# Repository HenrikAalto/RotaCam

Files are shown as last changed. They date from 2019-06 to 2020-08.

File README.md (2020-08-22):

# RotorCam180

Mit dem Projekt <strong>RotorCam180</strong> soll eine drehbare WabCam erstellt werden. 
Basierend auf einem <em>ESP32CAM Modul</em> in Verbindung mit einem RC-Servo soll zunächst ein um 180° schwenkbares Kameramodul entstehen. Die Befehle zur Steuerung soll via Telnet gesendet werden können.

<strong>Motivation:</strong>  
Zwar gibt es eine Vielzahl an Webcams auf dem Markt, doch sind die allermeisten Modelle inzwischen nur mit einer herstellereigenen Cloud nutzbar. Eine Eigenheit die mir persönlich überhaupt nicht zusagt ;-)

<strong>Idee:</strong>  
Seit einiger Zeit ist nun das ESP32Cam-Modul verfügbar (z.B. bei <a href="https://www.banggood.com/Geekcreit-ESP32-CAM-WiFi-bluetooth-Camera-Module-Development-Board-ESP32-With-Camera-Module-OV2640-p-1394679.html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">Banggods</a>)
Die kompakte Bauform ist ideal um sie, in Kombination mit einem <a href="https://www.banggood.com/4-X-Towerpro-MG90S-Metal-Gear-RC-Micro-Servo-p-961967.html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">RC-Servo</a>, eine drehbare Webcam aufzubauen.

<strong>Umsetzung:</strong>  
Die eigentliche WebCam-Funktionalität ist bereits in diversen Repositories zur Verfügung gestellt worden. In der ersten Version greife ich auf SourceCode von <a href="https://randomnerdtutorials.com">RandomNerd</a> zurück. An dieser Stelle vielen Dank an Rui Santos!

Die Steuerung des Servos erfolgt über eine Telnet-Verbindung. Nach Eingabe eines ‚?‘ erscheint die aktuelle Befehlsliste:

<pre><code>ESP32 - Cam Controller V0.1.1 (04-06-2019)  
_________________________________________________________  
Befehle  
Bxxx    - Blitz (Intensität 0 < xxx < 100)  
Rxxx    - Rotation (Winkel 0 < xxx < 180  
q       - Telnet-Sitzung beenden  
l       - Zustandslog aktivieren/deaktivieren 
i       - Initialisierung  
?       - Diese Liste  
</code></pre>

<em>Hinweis:  
Die Kommando-Buchstaben (zur Steuerung des Moduls) sind in Großbuchstaben, gefolgt von einem Parameter, Sitzungsbefehle in Kleinbuchstaben einzugeben.</em>

Um eine solide Einheit zu bilden, braucht die ganze Geschichte natürlich ein kompaktes Gehäuse. Das STL-Files des Moduls liegt <a href="https://github.com/HenrikAalto/RotorCam180/blob/master/WebCam-Träger_v2.0.stl">hier</a> ab lässt sich mit einem 3D-Drucker leicht herstellen. Es dient lediglich als Basisträger. Eine Abdeckung die das Ganze wetterfest und damit für den Außeneinsatz tauglich machen wird, ist in Planung…

<strong>Technischen Details:</strong>  
Um den Aufbau möglichst schlank zu gestalten, also ohne zusätzliche Platine (die weiteren Platz gebraucht hätte), ist das Gehäuse so entworfen, dass es auf der einen Seite das ESP32CAM-Modul aufnimmt 
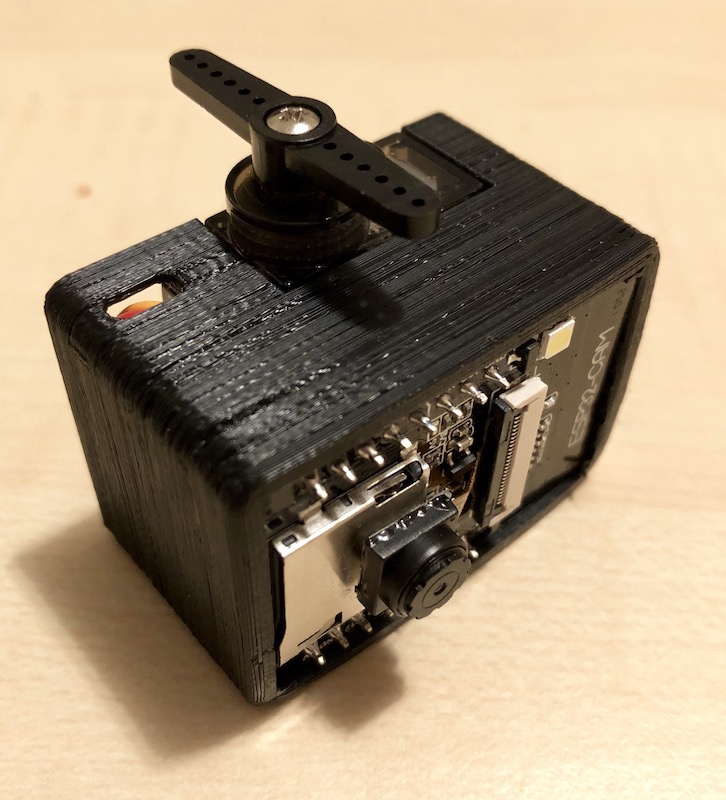
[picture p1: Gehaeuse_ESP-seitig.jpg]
  
und den Servo 
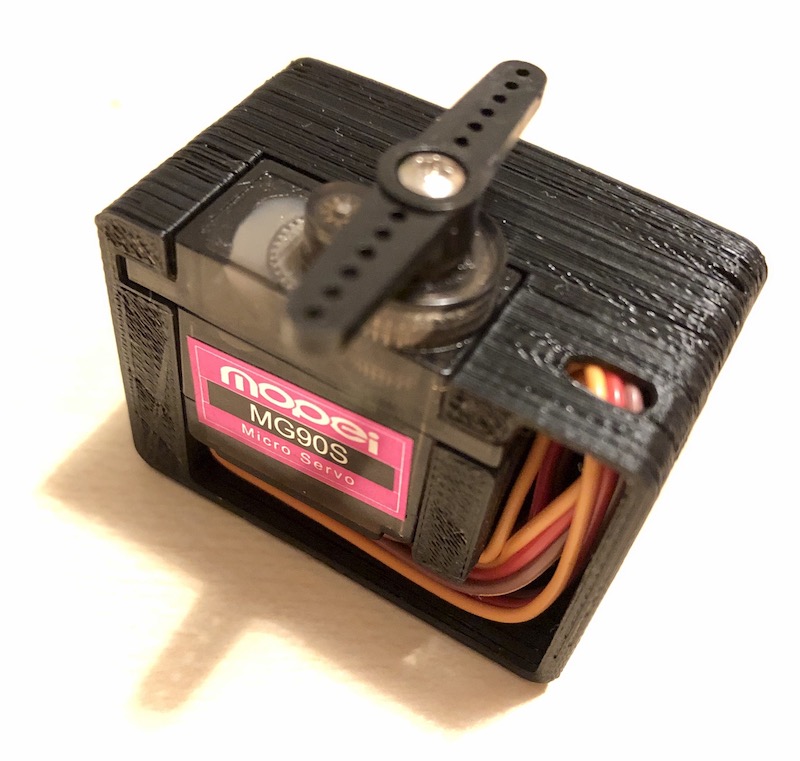
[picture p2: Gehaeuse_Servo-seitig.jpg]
  
auf der Anderen.  
Ein Durchbruch zu Vcc GND und Pin12 des ESP32CAM, in passender Größe für den Stecker des Servos ermöglichen die Verbindung von Beiden.  
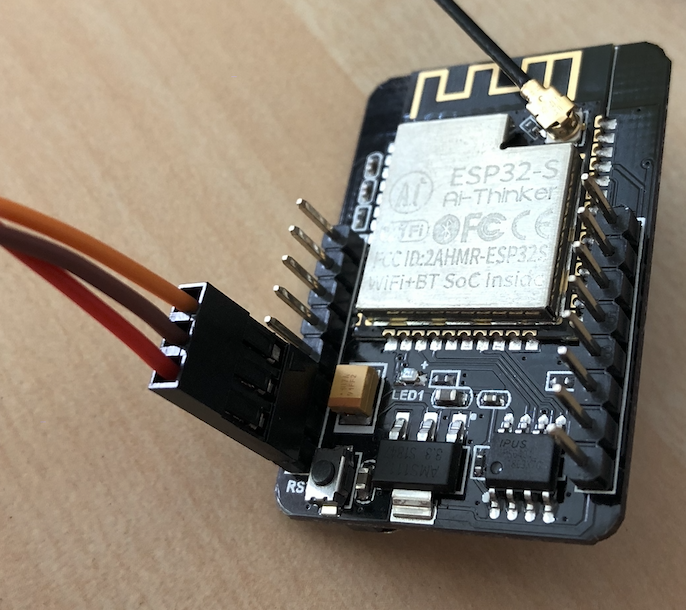
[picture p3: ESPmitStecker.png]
  
Leider passt die Pinbelegung des Steckers am Kabel Servomotor, bei diesem Modell nicht ab Werk nicht zu der am ESP32 CAM. Darum muss Vcc (rot) und GND (braun) am Stecker vertauscht werden. Es ist jedoch recht einfach die Kunststoffnasen des Steckers leicht aufzubiegen. 
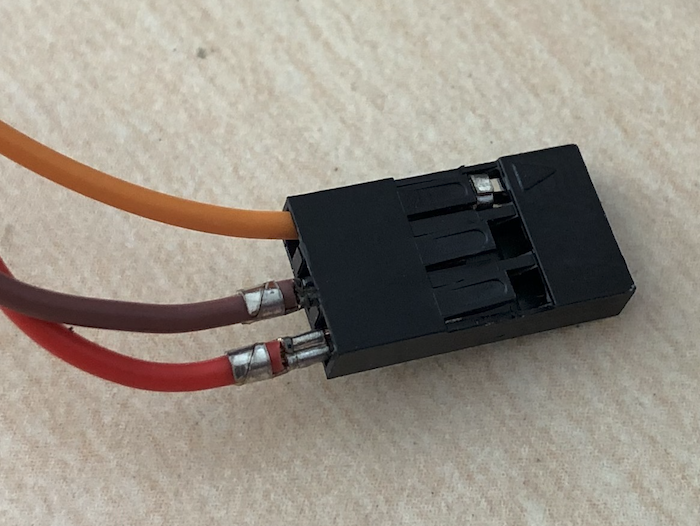
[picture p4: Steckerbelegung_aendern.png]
  
Dann können die beiden Metallstecker nach hinten herausgezogen und in der passenden Position wieder eingeschoben werden.
An die Anschlussleitung des Servos wird nun noch die Stromzuführung gelötet und durch die Bohrung des Gehäuses nach außen geführt. Der Rest des Kabels findet in der Aussparung des Gehäuses Platz.  
Das Drehkreuz des Servos wird nicht benötigt, da seine Achse später in die Grunplatte gesteckt und dort verschraubt wird. Es sollte also ausreichend Anschlussleitung eingeplant werden, damit die Drehung um 180° möglich ist.  
Dieses Foto zeigt nicht den letzten Designstand. Die aktuelle Version des Halters hat zusätzlich eine Öffnung um ggf. die Anschlussleitung einer externe Antenne nach außen führen zu können.
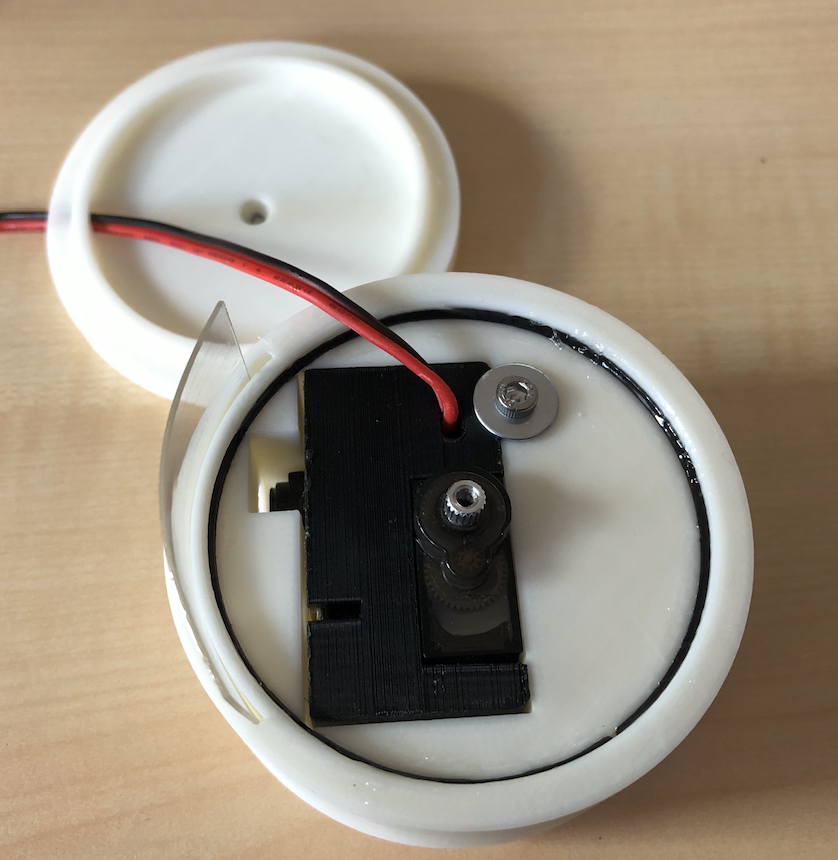
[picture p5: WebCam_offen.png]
  
Um das Trägermodul im <a href="https://github.com/HenrikAalto/RotorCam180/blob/master/WebCam-Abdeckung_v2.0.stl">Gehäuse</a> zu befestigen wird es mit einer Innensechskantschraube und eine Unterlagsscheibe fixiert. Das Gehäuse bietet auch die möglichkeit eine Kunststoffscheibe besser gesagt -folie einzuschieben, damit die Kameraoptik und die LED nicht der Witterung ausgesetzt sind. Um das erkennbar zu machen, habe ich die Scheibe für das Foto ein Stück weit herausgezogen. Eine Nut zum einschieben eines umlaufenden Dichtungsgummies (hier mit Flexifilament ausgeführt) ist ebenfalls vorhanden.  
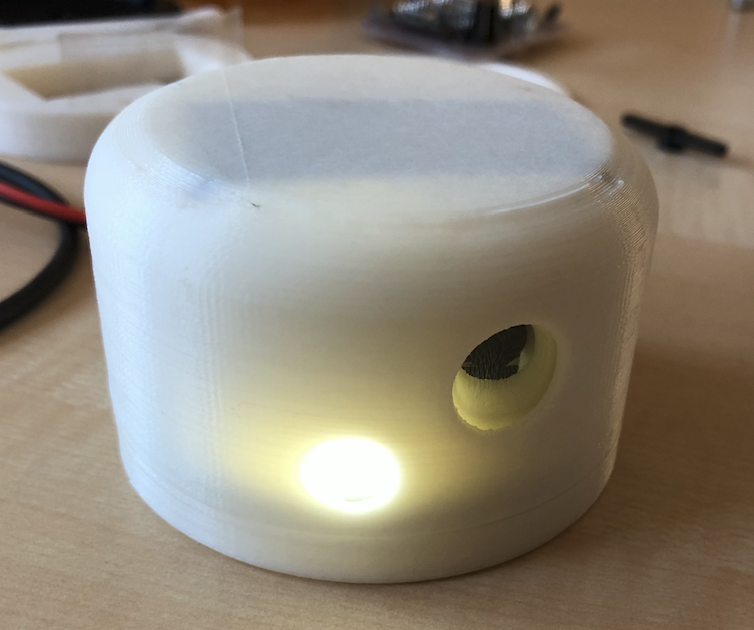
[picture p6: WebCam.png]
  
Hier das fertige, geschlossene Gehäuse (incl. <a href="https://github.com/HenrikAalto/RotorCam180/blob/master/WebCam-Standfuss_v2.0.stl">Grundplatte</a>).  

<strong>Hinweise:</strong>  
Bei dem von mir getesteten ESP32-Cam Modell war das WiFi-Signal sehr schwach. Entgegen meiner Erwartung war die interne Antenne nicht aktiv. Nach Verbinden mit einer externen WiFi-Antenne über den IPX-Stecker klappte alles prima und die Bildübertragung lief deutlich flüssiger (das war auch der Grund, das Design des Haltes nochmal anzupassen und eine Öffnung für das Antennenkaben hinzuzufügen). Auf der Seite von <a href="https://robotzero.one/esp32-cam-arduino-ide/">Robot Zero One</a> fand ich dann auch einen Hinweis, wie man erkennen kann welche Antennenkonfiguration einem geliefert wurde (On-Board vs IPEX Antenna). Bei einem anderem ESP32-Modul, das ich inzwischen erhalten habe, war (wie erwartet) die interne Antenne aktiv. Es war der gleiche Artikel, vom gleichen Liferanten - also besser immer erst mal unterm Mikroskop nachsehen.  
So siehts aus wenn der 0 Ohm Widerstand den externen Antennenanschluss aktiviert:
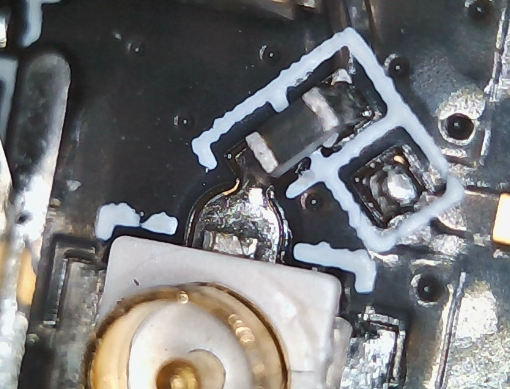
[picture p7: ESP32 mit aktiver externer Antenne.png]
  
...und so wenn die interne, aufgedruckte Antenne aktiv ist:  
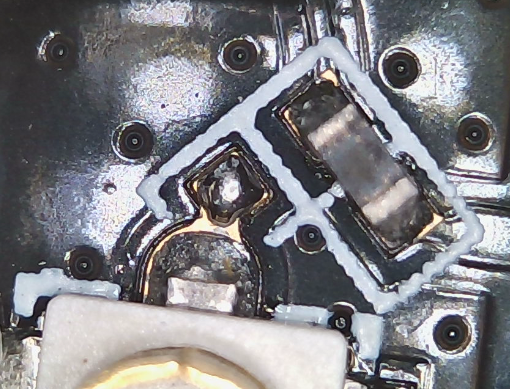
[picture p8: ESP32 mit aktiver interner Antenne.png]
  
Umlöten ist bei dem SMD-Fisselkram schwierig. Da es sich aber um einen 0 Ohm Widerstand handeln soll (also eine simple Verbindung), könnte ein Brücke aus Lötizinn zu internen Antenne genügen. Natürlich nur wenn zuvor das SMB-Bauteil ausgelötet wurde. Ich hab das aber nicht getestet sondern werde noch mit einigen externe Antennen testen. Wenn sich was brauchbares ergibt schreib ich's hier rein...  
Sehr hilfreich kann in dem Zusammenhang auch der unter 
https://github.com/SeeedDocument/forum_doc/raw/master/reg/ESP32_CAM_V1.6.pdf 
abliegende Schaltplan sein. Anhand dessen auch die etwas sonderbar anmutende Funktion des Pins4 (3,3V/5V) erklärlich wird. Es wirkt auf den ersten Blick unsinnig, dass im Plan der 3,3V- und der 5V-Anschluss jeweils über einen 0 Ohm Widerstand zusammengeschaltet werden. Schaut man sich das Board jedoch genauer an, erkennt man, dass der Hersteller nur einen (oder auch keinen) der 0 Ohm Widerstände eingelötet hat.  
Ursprünglich hatte ich überlegt dies zur Stromzuführung zu nutzen. Da dies trotz der oben erwähnten Erkentnisse jedoch nicht so richtig funktioniert wurde die Idee wieder verworfen.

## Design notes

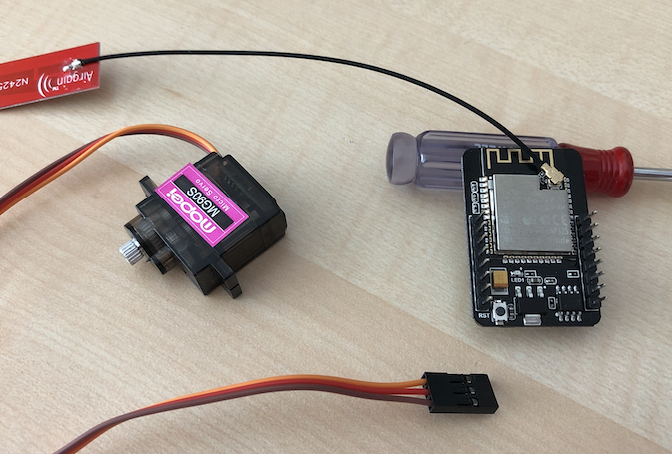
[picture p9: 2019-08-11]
ESPundServo.png

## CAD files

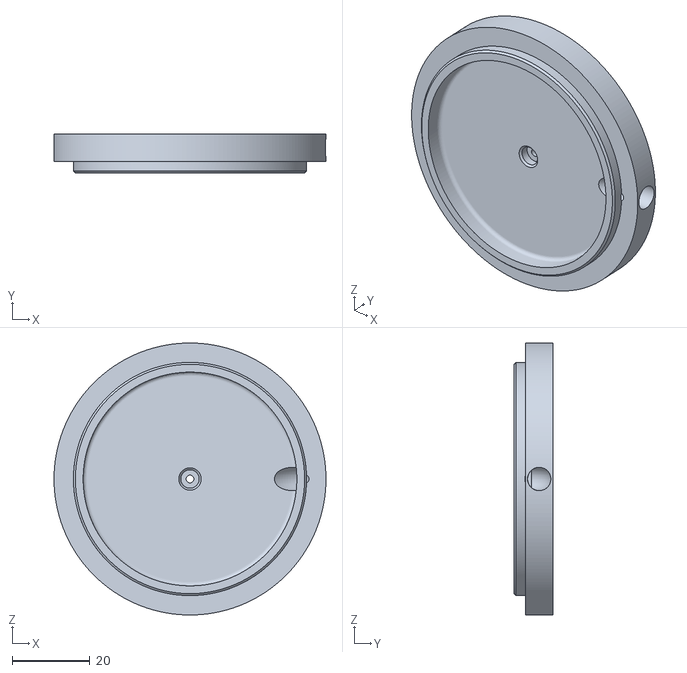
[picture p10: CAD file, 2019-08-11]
WebCam-Standfuss_v2.0.stl
70.0 x 10.0 x 70.0

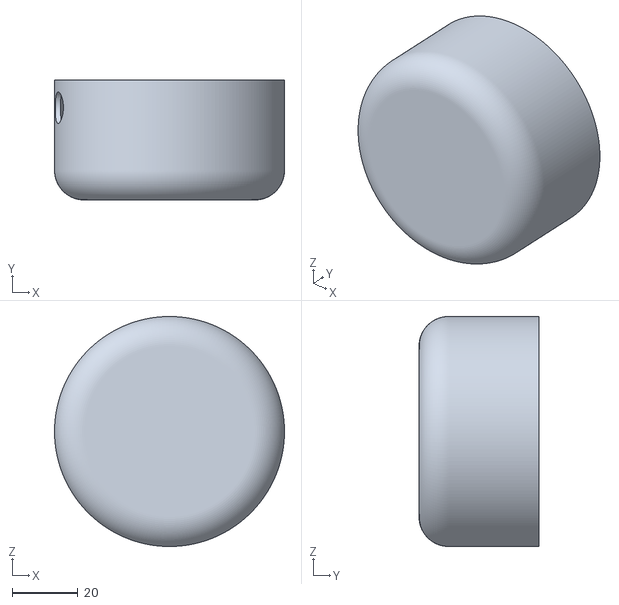
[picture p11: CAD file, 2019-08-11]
WebCam-Abdeckung_v2.0.stl
70.0 x 36.5 x 70.0

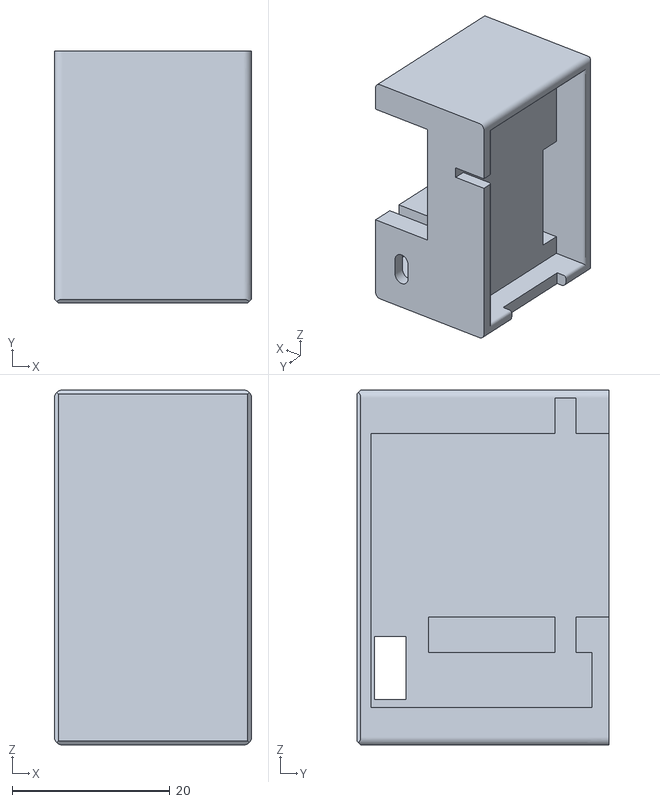
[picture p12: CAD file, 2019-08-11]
WebCam-Träger_v2.0.stl
25.0 x 32.0 x 45.0

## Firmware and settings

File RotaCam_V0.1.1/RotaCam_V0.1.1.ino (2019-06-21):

/*
  
  RotoCam
  
  Projektdetails unter
  https://github.com/HenrikAalto/RotaCam
  
  Vielen Dank an Rui Santos für die Umsetzung des WebCam-Moduls https://RandomNerdTutorials.com

  Bitte das ESP-Modul ggf. anpassen. 
  Ich habe bisher ausschließlich AI-Thinker Module benutzt.

  Diese Software steht jedem der es möchte zur Veränderung und Weiterentwicklung zur Verfügung.
  Ich gebe keinerlei Garantien für Funktionalität und/oder Zuverlässigkeit des Quellcodes

*/

#include "esp_camera.h"
#include "WiFi.h"
#include "esp_timer.h"
#include "img_converters.h"
#include "Arduino.h"
#include "fb_gfx.h"
#include "soc/soc.h"
#include "soc/rtc_cntl_reg.h"
#include "dl_lib.h"
#include "esp_http_server.h"

const char* Version = "V0.1.1 (04-06-2019)";   

// Das Programm ermöglicht zwei WiFi-Konfigurationen
// Beim Start wird erst versucht SSID1 zu verbinden, gelingt das nicht wird SSDI2 versucht
const char* ssid1 = "MySSID1";
const char* password1 = "PassphraseOfWiFi1";
const char* ssid2 = "MySSID2";
const char* password2 = "PassphraseOfWiFi2";

const int FlashPin =  4;                  // Pin für das Blitzlicht
const int FlashChannel = 5;               // PWM-Kanal des Blitzes

const int myServoPin =  12;               // Pin für das Servo
const long myServoMax =  114;             // Maximalwinkel für das Servo
const long myServoMin =  13;              // Minimalwinkel für das Servo
const int myServoChannel = 6;             // PWM-Kanal des Servos
const int myServoVerstellbereich = 205;   // Gradzahl um die der Servo verstellt werden kann
const int myServoPause = 25;              // Standard Pausenzeit nach Verstellung des Servos

// Variablen

long gegenwaertiger_Zustand = 1;          // Variable für den vollständigen Automaten
long zukuenftigertiger_Zustand = 1;       // Variable für den vollständigen Automaten

int LogLevel = 0;                         // Variable um Log Level einzustellen (0=keine, 1=Zustandsausgabe über Seriell)

int inByte = 0;                           // Variable zu Anzeige über welche Schnittstelle Daten eintreffen
int flash = 0;                            //Blitzlicht 0=aus 1=ein

int MyServoPosition = myServoMin;         //Servoposition

uint8_t TelnetSession;                    // Sitzungsnr. Telnet

int i;
char command;
char inputString [5];

#define MAX_SRV_CLIENTS 1 

#define PART_BOUNDARY "123456789000000000000987654321"

#define CAMERA_MODEL_AI_THINKER
//#define CAMERA_MODEL_M5STACK_PSRAM
//#define CAMERA_MODEL_WROVER_KIT

#if defined(CAMERA_MODEL_WROVER_KIT)
  #define PWDN_GPIO_NUM    -1
  #define RESET_GPIO_NUM   -1
  #define XCLK_GPIO_NUM    21
  #define SIOD_GPIO_NUM    26
  #define SIOC_GPIO_NUM    27  
  #define Y9_GPIO_NUM      35
  #define Y8_GPIO_NUM      34
  #define Y7_GPIO_NUM      39
  #define Y6_GPIO_NUM      36
  #define Y5_GPIO_NUM      19
  #define Y4_GPIO_NUM      18
  #define Y3_GPIO_NUM       5
  #define Y2_GPIO_NUM       4
  #define VSYNC_GPIO_NUM   25
  #define HREF_GPIO_NUM    23
  #define PCLK_GPIO_NUM    22

#elif defined(CAMERA_MODEL_M5STACK_PSRAM)
  #define PWDN_GPIO_NUM     -1
  #define RESET_GPIO_NUM    15
  #define XCLK_GPIO_NUM     27
  #define SIOD_GPIO_NUM     25
  #define SIOC_GPIO_NUM     23 
  #define Y9_GPIO_NUM       19
  #define Y8_GPIO_NUM       36
  #define Y7_GPIO_NUM       18
  #define Y6_GPIO_NUM       39
  #define Y5_GPIO_NUM        5
  #define Y4_GPIO_NUM       34
  #define Y3_GPIO_NUM       35
  #define Y2_GPIO_NUM       32
  #define VSYNC_GPIO_NUM    22
  #define HREF_GPIO_NUM     26
  #define PCLK_GPIO_NUM     21

#elif defined(CAMERA_MODEL_AI_THINKER)
  #define PWDN_GPIO_NUM     32
  #define RESET_GPIO_NUM    -1
  #define XCLK_GPIO_NUM      0
  #define SIOD_GPIO_NUM     26
  #define SIOC_GPIO_NUM     27
  #define Y9_GPIO_NUM       35
  #define Y8_GPIO_NUM       34
  #define Y7_GPIO_NUM       39
  #define Y6_GPIO_NUM       36
  #define Y5_GPIO_NUM       21
  #define Y4_GPIO_NUM       19
  #define Y3_GPIO_NUM       18
  #define Y2_GPIO_NUM        5
  #define VSYNC_GPIO_NUM    25
  #define HREF_GPIO_NUM     23
  #define PCLK_GPIO_NUM     22
#else
  #error "Kein Kameramodul ausgewählt!"
#endif

static const char* _STREAM_CONTENT_TYPE = "multipart/x-mixed-replace;boundary=" PART_BOUNDARY;
static const char* _STREAM_BOUNDARY = "\r\n--" PART_BOUNDARY "\r\n";
static const char* _STREAM_PART = "Content-Type: image/jpeg\r\nContent-Length: %u\r\n\r\n";

httpd_handle_t stream_httpd = NULL;

static esp_err_t stream_handler(httpd_req_t *req){
  camera_fb_t * fb = NULL;
  esp_err_t res = ESP_OK;
  size_t _jpg_buf_len = 0;
  uint8_t * _jpg_buf = NULL;
  char * part_buf[64];

  res = httpd_resp_set_type(req, _STREAM_CONTENT_TYPE);
  if(res != ESP_OK){
    return res;
  }

  while(true){
    fb = esp_camera_fb_get();
    if (!fb) {
      Serial.println("Bilderfassung fehlgeschlagen!");
      res = ESP_FAIL;
    } else {
      if(fb->width > 400){
        if(fb->format != PIXFORMAT_JPEG){
          bool jpeg_converted = frame2jpg(fb, 80, &_jpg_buf, &_jpg_buf_len);
          esp_camera_fb_return(fb);
          fb = NULL;
          if(!jpeg_converted){
            Serial.println("JPEG Kompression fehlgeschlagen!");
            res = ESP_FAIL;
          }
        } else {
          _jpg_buf_len = fb->len;
          _jpg_buf = fb->buf;
        }
      }
    }
    if(res == ESP_OK){
      size_t hlen = snprintf((char *)part_buf, 64, _STREAM_PART, _jpg_buf_len);
      res = httpd_resp_send_chunk(req, (const char *)part_buf, hlen);
    }
    if(res == ESP_OK){
      res = httpd_resp_send_chunk(req, (const char *)_jpg_buf, _jpg_buf_len);
    }
    if(res == ESP_OK){
      res = httpd_resp_send_chunk(req, _STREAM_BOUNDARY, strlen(_STREAM_BOUNDARY));
    }
    if(fb){
      esp_camera_fb_return(fb);
      fb = NULL;
      _jpg_buf = NULL;
    } else if(_jpg_buf){
      free(_jpg_buf);
      _jpg_buf = NULL;
    }
    if(res != ESP_OK){
      break;
    }
    //Serial.printf("MJPG: %uB\n",(uint32_t)(_jpg_buf_len));
  }
  return res;
}

WiFiServer TelnetServer(23);
WiFiClient TelnetServerClients[MAX_SRV_CLIENTS];

void startCameraServer(){
  httpd_config_t config = HTTPD_DEFAULT_CONFIG();
  config.server_port = 80;

  httpd_uri_t index_uri = {
    .uri       = "/",
    .method    = HTTP_GET,
    .handler   = stream_handler,
    .user_ctx  = NULL
  };
  
  //Serial.printf("Starte Webserver an Port: '%d'\n", config.server_port);
  if (httpd_start(&stream_httpd, &config) == ESP_OK) {
    httpd_register_uri_handler(stream_httpd, &index_uri);
  }
}

void SetServoPos(float winkel)
{
    int i = 0;
    
    // Übersetzen des Winkels in eine Pulsweite anhand Max/Min
    uint32_t duty = ((winkel/(myServoVerstellbereich))*(myServoMax-myServoMin)) + myServoMin; 
    
    if (inByte == 2) {
      Serial.print("Servo-Winkel: ");
        }
    if (inByte == 1) {
      TelnetServerClients[TelnetSession].print("Servo-Winkel: ");
    }
    if (MyServoPosition > duty) {
      for (i = MyServoPosition ; i >= duty; i -= 1) { 
        ledcWrite(myServoChannel, i);  
       delay(myServoPause); 
      }
    } else {
      for (i = MyServoPosition ; i <= duty; i += 1) { 
        ledcWrite(myServoChannel, i);  
       delay(myServoPause); 
      }
    }
    if (inByte == 2) {
      Serial.print(winkel); 
      Serial.print(" (");   
      Serial.print(duty);
      Serial.println(") Grad (Zahlwert)");
    }
    if (inByte == 1) {
      TelnetServerClients[TelnetSession].print(winkel); 
      TelnetServerClients[TelnetSession].print(" (");   
      TelnetServerClients[TelnetSession].print(duty);
      TelnetServerClients[TelnetSession].println(") Grad (Zahlwert)");
    }

    MyServoPosition = duty;
    delay(200);
//    ledcSetup(myServoChannel, 0, 8);
}

void setup() {
  WRITE_PERI_REG(RTC_CNTL_BROWN_OUT_REG, 0); //disable brownout detector
 
  Serial.begin(115200);
  Serial.setDebugOutput(false);
}

void loop() {
  switch (gegenwaertiger_Zustand) {
    
    case 1:   //Kamera initialisieren
      {
        camera_config_t config;
        config.ledc_channel = LEDC_CHANNEL_0;
        config.ledc_timer = LEDC_TIMER_0;
        config.pin_d0 = Y2_GPIO_NUM;
        config.pin_d1 = Y3_GPIO_NUM;
        config.pin_d2 = Y4_GPIO_NUM;
        config.pin_d3 = Y5_GPIO_NUM;
        config.pin_d4 = Y6_GPIO_NUM;
        config.pin_d5 = Y7_GPIO_NUM;
        config.pin_d6 = Y8_GPIO_NUM;
        config.pin_d7 = Y9_GPIO_NUM;
        config.pin_xclk = XCLK_GPIO_NUM;
        config.pin_pclk = PCLK_GPIO_NUM;
        config.pin_vsync = VSYNC_GPIO_NUM;
        config.pin_href = HREF_GPIO_NUM;
        config.pin_sscb_sda = SIOD_GPIO_NUM;
        config.pin_sscb_scl = SIOC_GPIO_NUM;
        config.pin_pwdn = PWDN_GPIO_NUM;
        config.pin_reset = RESET_GPIO_NUM;
        config.xclk_freq_hz = 20000000;
        config.pixel_format = PIXFORMAT_JPEG; 
        config.frame_size = FRAMESIZE_UXGA;
        config.jpeg_quality = 10;
        config.fb_count = 2;
  
        esp_err_t err = esp_camera_init(&config);
        if (err != ESP_OK) {
          Serial.printf("Kamerainitialisierung fehlgeschlagen mit Error 0x%x", err);
          zukuenftigertiger_Zustand = 999;
        } else {
          zukuenftigertiger_Zustand = 2;
        }
      }
      break;

    case 2:   // PWM für Blitzlichr und Servo initialisieren
      {
        //Servo:  chanel 1, 166Hz, 8Bit;
        ledcSetup(myServoChannel, 166, 8);
        ledcAttachPin(myServoPin, myServoChannel);
        ledcWrite(myServoChannel, myServoMin);   //Servo in 0 Grad Stellung
        delay(1000);
              
        //Blitzlicht: Kanal 2, 500Hz, 8Bit;
        ledcSetup(FlashChannel, 500, 8);
        ledcAttachPin(FlashPin, FlashChannel);
        ledcWrite(FlashChannel, 0);            // LED aus

        zukuenftigertiger_Zustand = 3;
      }
      break;
  
    case 3:   // Initialisierung Blitze und Servo testen 
      { 
        Serial.print("Blitz-LED-Test...");
        ledcWrite(FlashChannel, 255); // LED zum Start an
        delay(500);
        ledcWrite(FlashChannel, 0);  // LED aus
        Serial.println(" fertig.");
       
        Serial.println("Servo-Test...");
        SetServoPos(180);
        delay(200);
        SetServoPos(10);
        Serial.println("fertig.");
        
        zukuenftigertiger_Zustand = 4;
      }
      break;
      
    case 4:   // erste WiFi-Verbindung aufbauen
      {
        int i=0;
        
        // Wi-Fi connection
        Serial.print("WiFi Verbindung zu ");
        Serial.print(ssid1);
        Serial.print(" wird aufgebaut...");
        WiFi.begin(ssid1, password1);
        while ((WiFi.status() != WL_CONNECTED) and (i != 10)) {
          ledcWrite(FlashChannel, 1); // LED an
          delay(10);
          ledcWrite(FlashChannel, 0); // LED aus
          delay(500);
          i=i+1;
          Serial.print(".");
        }
        if (WiFi.status() == WL_CONNECTED) {
          Serial.println(" fertig.");
          zukuenftigertiger_Zustand = 8;
        } else {
          Serial.println(" fehlgeschlagen!!!");
          zukuenftigertiger_Zustand = 5;
        }
        
      }
      break;
      
    case 5:   // Wifi abschalten wenn erste Verbindung nicht zustande kam
      {
        Serial.print("WiFi wird abgeschaltet...");
        WiFi.mode(WIFI_OFF);
        delay(2000);
        Serial.println(" fertig.");
        zukuenftigertiger_Zustand = 6;
      }
      break;

    case 6:   // zweite WiFi-Verbindung  aufbauen
      {
        int i=0;
        
        // Wi-Fi connection
        Serial.print("WiFi Verbindung zu ");
        Serial.print(ssid2);
        Serial.print(" wird aufgebaut...");
        WiFi.begin(ssid2, password2);
        while ((WiFi.status() != WL_CONNECTED) and (i != 10)) {
          ledcWrite(FlashChannel, 10); // LED an
          delay(10);
          ledcWrite(FlashChannel, 0); // LED aus
          delay(500);
          i=i+1;
          Serial.print(".");
        }
        if (WiFi.status() == WL_CONNECTED) {
          Serial.println(" fertig.");
          zukuenftigertiger_Zustand = 8;
        } else {
          Serial.println(" fehlgeschlagen!!!");
          zukuenftigertiger_Zustand = 7;
        }
        
      }
      break;

    case 7:   // Wifi abschalten wenn zweite Verbindung nicht zustande kam
      {
        Serial.print("WiFi wird abgeschaltet...");
        WiFi.mode(WIFI_OFF);
        delay(2000);
        Serial.println(" fertig.");
        zukuenftigertiger_Zustand = 999;
      }
      break;

    case 8:   // Videostream einschalten
      {
        Serial.print("Kamerastream wird gestartet...");
        startCameraServer();
        Serial.print(" fertig.    (http://");
        Serial.print(WiFi.localIP());
        Serial.println(")");
        zukuenftigertiger_Zustand = 9;
      }
      break;

    case 9:   // Telnetserver einschalten
      {
        Serial.print("Telnetserver wird gestartet...");
        TelnetServer.begin();
        TelnetServer.setNoDelay(true);
        Serial.print(" fertig.    (");
        Serial.print(WiFi.localIP());
        Serial.println(")");
        zukuenftigertiger_Zustand = 90;
      }
      break;

    case 90:    // Testen ob noch ungenutzte Sitzungen offen stehen und diese ggf. schließen
      {   inByte = 0;     
          for(i = 0; i < MAX_SRV_CLIENTS; i++)
          {
            if (TelnetServerClients[i] && !TelnetServerClients[i].connected())
            {
              Serial.print("Client disconnected ... terminate session "); Serial.println(i+1); 
              TelnetServerClients[i].stop();
            }
          }
          zukuenftigertiger_Zustand = 91;
      }
      break;

     case 91:    // Prüfen ob Clients mit dem TelnetServer Verbindung aufgenommen haben
       { 
         if (TelnetServer.hasClient())
         {
            zukuenftigertiger_Zustand = 92;
         } else {
            zukuenftigertiger_Zustand = 94;   // Seriellen Input auswerten
         } 
       }
      break;

    case 92:    // Sitzungen prüfen uund neue Clienten begrüßen
      {                            
        for(i = 0; i < MAX_SRV_CLIENTS; i++) // Nach neuen Sitzungen suchen und diese begrüßen
        {
          Serial.print("Teste Telnet-Sitzungen "); Serial.println(i+1);
          
          // find free socket
          if (!TelnetServerClients[i])
          {
            TelnetServerClients[i] = TelnetServer.available(); 
            
            Serial.print("Neue Telnetcliens haben Verbindung aufgebaut "); Serial.println(i+1);
            
            TelnetServerClients[i].flush();  // Input buffer leeren
            TelnetServerClients[i].print("ESP32 - Cam Controller ");
            TelnetServerClients[i].println(Version);
           
            TelnetServerClients[i].print("Millisekunden seit dem Start des Moduls: ");
            TelnetServerClients[i].println(millis());
            
            TelnetServerClients[i].print("Freies RAM: ");
            TelnetServerClients[i].println(ESP.getFreeHeap());
      
            TelnetServerClients[i].println("----------------------------------------------------------------");
            zukuenftigertiger_Zustand = 94;
            break;
          }
          else
          {
            Serial.println("Sitzung wird bereits genutzt.");
            zukuenftigertiger_Zustand = 93;
          }
        }
      }
      break;

    case 93:    // Maximale Sitzungszahl erreicht, neue ablehnen
      {
        Serial.println("Maximale Anzahl der Telnet-Sitzung erreicht!");
        TelnetServer.available().stop();                           
        zukuenftigertiger_Zustand = 94;      }
      break;

    case 94:   // Daten aus den Telnetsitzungn lesen.
      {
        zukuenftigertiger_Zustand = 95;  // Vordefinierter zukünftiger zustand für den Fall, dass keine Daten vorliegen
        for(i = 0; i < MAX_SRV_CLIENTS; i++)
          {
            if (TelnetServerClients[i] && TelnetServerClients[i].connected())
            {
              if(TelnetServerClients[i].available())
              { 
                command = TelnetServerClients[i].read();
                int c = 0;
                while(TelnetServerClients[i].available())
                {
                  inputString[c] = TelnetServerClients[i].read();
                  c++;
                }
                inByte=1;
                zukuenftigertiger_Zustand = 100;
              }
            }
          }
       }
      break;

    case 95:   // Serielle Schnittstelle auf eingehende Daten überwachen
      {
        if (Serial.available()) {
          command = Serial.read();
          int c = 0;
          while(Serial.available())
          {
            inputString [c] = Serial.read();
            c++;
          }
          inByte=2;
          zukuenftigertiger_Zustand = 100;
        }
        else {
          zukuenftigertiger_Zustand = 90;
        }       
      }
      break;
      
    case 100:    // Auf der seriellen Schnittstelle eingetroffene Zeichen auswerten
      {
        switch (command) {
          case 'B':
            {
              zukuenftigertiger_Zustand = 110;  //Kommando für Flash
            }
            break;

          case 'i':
            {
              zukuenftigertiger_Zustand = 999;  //Kommando für Reboot
            }
            break;

          case 'R':
            {
              zukuenftigertiger_Zustand = 210;  //Kommando für Rotation
            }
            break;

          case 'l':
            {
              zukuenftigertiger_Zustand = 998;  //Kommando im Logs zu aktivieren/deaktivieren
            }
            break;
            
          case 'q':
            {
              zukuenftigertiger_Zustand = 800;  //Kommando zum beenden der Telnetsession
            }
            break;
            
          case '?':
            {
              if (inByte == 2) {                
                Serial.print("ESP32 - Cam Controller ");
                Serial.println(Version);
                Serial.println("______________________________________________________");
                Serial.println("Befehle");
                Serial.println("Bxxx    - Blitz    (Intensität 0 < xxx < 100)");
                Serial.print("Rxxx    - Rotation (Winkel 0 < xxx < ");
                Serial.print(myServoVerstellbereich);
                Serial.println(")");
                Serial.println("l       - Zustandslog aktivieren/deaktivieren");
                Serial.println("i       - Initialisierung");
                Serial.println("?       - Diese Liste");
              }              
              if (inByte == 1) {
                TelnetServerClients[TelnetSession].print("ESP32 - Cam Controller ");
                TelnetServerClients[TelnetSession].print(Version);
                TelnetServerClients[TelnetSession].println("");
                TelnetServerClients[TelnetSession].println("______________________________________________________");
                TelnetServerClients[TelnetSession].println("Befehle");
                TelnetServerClients[TelnetSession].println("Bxxx    - Blitz    (Intensität 0 < xxx < 100)");
                TelnetServerClients[TelnetSession].print("Rxxx    - Rotation (Winkel 0 < xxx < ");
                TelnetServerClients[TelnetSession].print(myServoVerstellbereich);
                TelnetServerClients[TelnetSession].println(")");
                TelnetServerClients[TelnetSession].println("q       - Telnet-Sitzung beenden");
                TelnetServerClients[TelnetSession].println("l       - Zustandslog aktivieren/deaktivieren");
                TelnetServerClients[TelnetSession].println("i       - Initialisierung");
                TelnetServerClients[TelnetSession].println("?       - Diese Liste");                              
              }
              zukuenftigertiger_Zustand = 90;
            }
            break;
            
          default: {
              // Ungültiger Sequenzbeginn -> ignorieren
              zukuenftigertiger_Zustand = 90;
            }
            break;
        }
      }
      break;
      
    case 110:    // Blitz-LED steuern
      {
        int op = atoi(inputString);
        
        if (op <= 100) {                  
          uint32_t duty = (op*254)/100;                           
          ledcWrite(FlashChannel, duty);
          if (inByte == 2) {
            Serial.print("Blitzlicht auf ");
            Serial.print(op);
            Serial.println("% gesetzt");
          }
          if (inByte == 1) {
            TelnetServerClients[TelnetSession].print("Blitzlicht auf ");
            TelnetServerClients[TelnetSession].print(op);
            TelnetServerClients[TelnetSession].println("% gesetzt"); 
          }
        } else {
          if (inByte == 2) {
            Serial.print("Wert (");
            Serial.print(op);
            Serial.println(") außerhalb des möglichen Bereichs!"); 
          }
          if (inByte == 1) {
            TelnetServerClients[TelnetSession].print("Wert (");
            TelnetServerClients[TelnetSession].print(op);
            TelnetServerClients[TelnetSession].println(") außerhalb des möglichen Bereichs!"); 
          }
        }
        zukuenftigertiger_Zustand = 90;
      }
      break;

    case 210:    // Servo Steuern
      {
        int op = atoi(inputString);
        
        if (op <= myServoVerstellbereich) {
          SetServoPos(op);
        } else {
          if (inByte == 2) {
            Serial.print("Wert (");
            Serial.print(op);
            Serial.println(") außerhalb des möglichen Bereichs!"); 
          }
          if (inByte == 1) {
            TelnetServerClients[TelnetSession].print("Wert (");
            TelnetServerClients[TelnetSession].print(op);
            TelnetServerClients[TelnetSession].println(") außerhalb des möglichen Bereichs!"); 
          }
        }
        zukuenftigertiger_Zustand = 90;
      }
      break;
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

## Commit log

2019-06-21 Inhalt wird in ReadMe überführt
2019-06-21 Formatierung des Textes
2019-06-21 INO-File zum Upload mit Arduino-IDE
    Der Upload in das ESP32CAM-Modul kann nur über eine serielle Schnittstelle erfolgen. Es ist dazu erforderlich GPIO0 mit Masse zu verbinden und dann den Reset-Knopf am Modul zu drücken. Dadurch schaltet es in den Empfangsmodus und nimmt die Uploaddaten an.
    [RotaCam_V0.1.1.ino]
2019-07-03 Fotos des kompletten Innenmoduls
2019-07-16 Vergrößerungen ESP32 Antenne
    Zur Verdeutlichung der Beschattung der internen Antenne bzw. des Antennenanschlusses für die externe Antenne
2019-08-11 WebCam
    Fertiges WebCam Gehäuse (LED-Beleuchtung aktiv)
2019-08-11 Fotos vom Zusammenbau und der fertigen Webcam
2019-08-11 ESP32-CAM mit Markierung der drei benötigten Pins
2019-08-11 Anschluss Pins ESP32-CAM für Servo
2019-08-11 ESP32-Cam und Servo mit originaler Steckerbelegung
2019-08-11 Pinbelegung des Steckers verändern
2019-08-11 ESP32-Cam mit Stecker
    ESP32-Cam mit korrekt beschaltetem Stecker des Servos
2019-08-11 Steckerbeschaltung
    Detailfotos zu Änderung der Steckerbeschaltung
2019-08-11 Webcam-Träger (v2)
    [WebCam-Träger_v2.0.stl]
2019-08-11 WebCam Abdeckung (v2)
    [WebCam-Abdeckung_v2.0.stl]
2019-08-11 WebCam Standfuß (v2)
    [WebCam-Standfuss_v2.0.stl]
2019-08-11 Veraltete Version
    [Webcam-Träger V1.4.stl]
2019-08-11 Verlinkungen zu STL-Gehäusedaten hinzugefügt
